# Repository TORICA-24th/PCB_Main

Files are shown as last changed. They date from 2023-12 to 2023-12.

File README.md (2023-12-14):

# PCB_Main
メイン電装部のPCBデータです．24代のメイン電装は2層構成になっており，上層をPCB_Main1,下層をPCB_Main2として設計しています．

# 使用している部品，フットプリント
テキスト印字→◯の部品は基板上にテキスト(ICS-Boardなど)を印字してください．
リファレンス印字→◯の部品は基板上にリファレンス(D1など)を印字してください．
## PCB_Main1
|リファレンス|部品|フットプリント|テキスト印字|リファレンス印字|
|:---:|:---:|:---:|:---:|:---:|
|D1~D8|[整流ダイオード](https://akizukidenshi.com/catalog/g/gI-08327/)|Diode_THT:D_A-405_P10.16mm_Horizontal|✕|✕|
|D9~D14|[LED](https://akizukidenshi.com/catalog/g/gI-06247/)|LED_THT:LED_D5.0mm|◯|✕|
|M78AR05-1~M78AR05-4|[DCDCコンバータ(5V0.5A)](https://akizukidenshi.com/catalog/g/gM-07179/)|Converter_DCDC:Converter_DCDC_RECOM_R-78E-0.5_THT|✕|◯|
|M78AR033-1|[DCDCコンバータ(3.3V0.5A)](https://akizukidenshi.com/catalog/g/gM-07178/)|Converter_DCDC:Converter_DCDC_RECOM_R-78E-0.5_THT|✕|◯|
|XH1~XH6|[XHコネクタ](https://akizukidenshi.com/catalog/g/gC-12842/)|((n)はピン数に合わせて)Connector_JST:JST_XH_S4B-XH-A_1x0(n)_P2.50mm_Horizontal|◯|✕|
|U1|[Raspberry Pi Pico](https://akizukidenshi.com/catalog/g/gM-16132/)|SamacSys_Parts:RPi_Pico_SMD_TH|✕|✕|
|U2|[BNO055](https://akizukidenshi.com/catalog/g/gK-16996/)|AE-BNO055:AE-BNO055|◯|✕|
|U3|[DPS310](https://www.switch-science.com/products/6286)|DPS310:DPS310|◯|✕|
|ICS-Board1|[ICS変換基板](https://www.amazon.co.jp/dp/B07XYZWJGD)|ICS:ICS|✕|✕|
|ICS-SW1A|[トグルスイッチ 3P1回路2接点](https://akizukidenshi.com/catalog/g/gP-12406/)|Connector_PinHeader_2.54mm:PinHeader_1x03_P2.54mm_Vertical|◯|✕|
|C1|[電解コンデンサ](https://akizukidenshi.com/catalog/g/gP-17897/)|Capacitor_THT:CP_Radial_D5.0mm_P2.50mm|✕|◯|

補足  
- 配置は別で送った配置図で指定されているものはそれに従ってください
- 四隅にM3のネジ穴を開けてください

## PCB_Main2
|リファレンス|部品|フットプリント|テキスト印字|リファレンス印字|

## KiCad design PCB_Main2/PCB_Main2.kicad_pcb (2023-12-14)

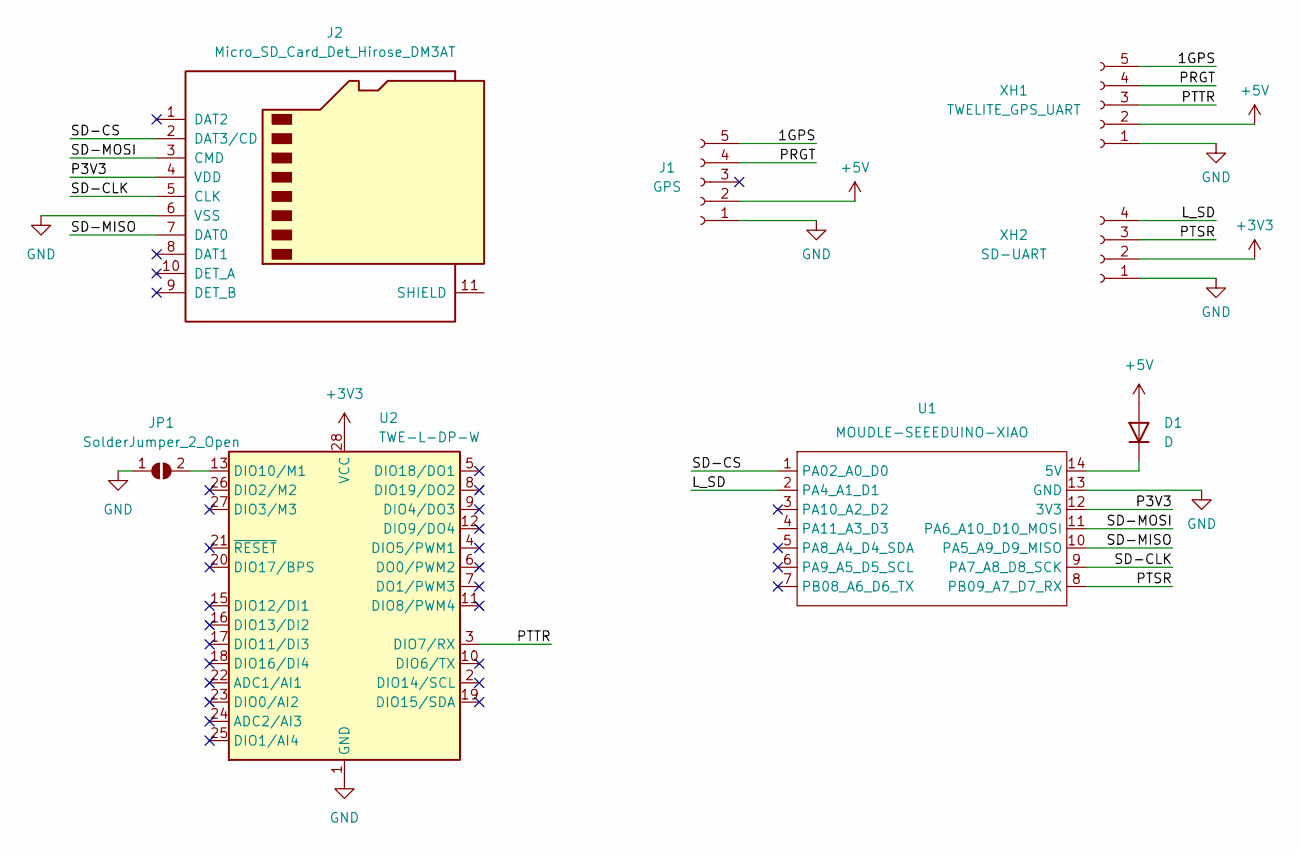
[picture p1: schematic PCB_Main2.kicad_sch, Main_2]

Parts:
D1: D; D_A-405_P10.16mm_Horizontal
J1: GPS; JST_XH_S5B-XH-A_1x05_P2.50mm_Horizontal
J2: Micro_SD_Card_Det_Hirose_DM3AT; microSD_AE-MICRO-SD-DIP
JP1: SolderJumper_2_Open; SolderJumper-2_P1.3mm_Open_RoundedPad1.0x1.5mm
U1: MOUDLE-SEEEDUINO-XIAO; MOUDLE14P-2.54-21X17.8MM
U2: TWE-L-DP-W; DIP-28_W15.24mm
XH1: TWELITE_GPS_UART; JST_XH_S5B-XH-A_1x05_P2.50mm_Horizontal
XH2: SD-UART; JST_XH_S4B-XH-A_1x04_P2.50mm_Horizontal

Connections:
+3V3: U2.28 (VCC), XH2.2
+5V: D1.2 (A), J1.2, XH1.2
/1GPS: J1.5, XH1.5
/L_SD: U1.2 (PA4_A1_D1), XH2.4
/P3V3: J2.4 (VDD), U1.12 (3V3)
/PRGT: J1.4, XH1.4
/PTSR: U1.8 (PB09_A7_D7_RX), XH2.3
/PTTR: U2.3 (DIO7/RX), XH1.3
/SD-CLK: J2.5 (CLK), U1.9 (PA7_A8_D8_SCK)
/SD-CS: J2.2 (DAT3/CD), U1.1 (PA02_A0_D0)
/SD-MISO: J2.7 (DAT0), U1.10 (PA5_A9_D9_MISO)
/SD-MOSI: J2.3 (CMD), U1.11 (PA6_A10_D10_MOSI)
GND: J1.1, J2.6 (VSS), JP1.1 (A), U1.13 (GND), U2.1 (GND), U2.14 (GND), XH1.1, XH2.1
unnamed: D1.1 (K), U1.14 (5V)
unnamed: JP1.2 (B), U2.13 (DIO10/M1)

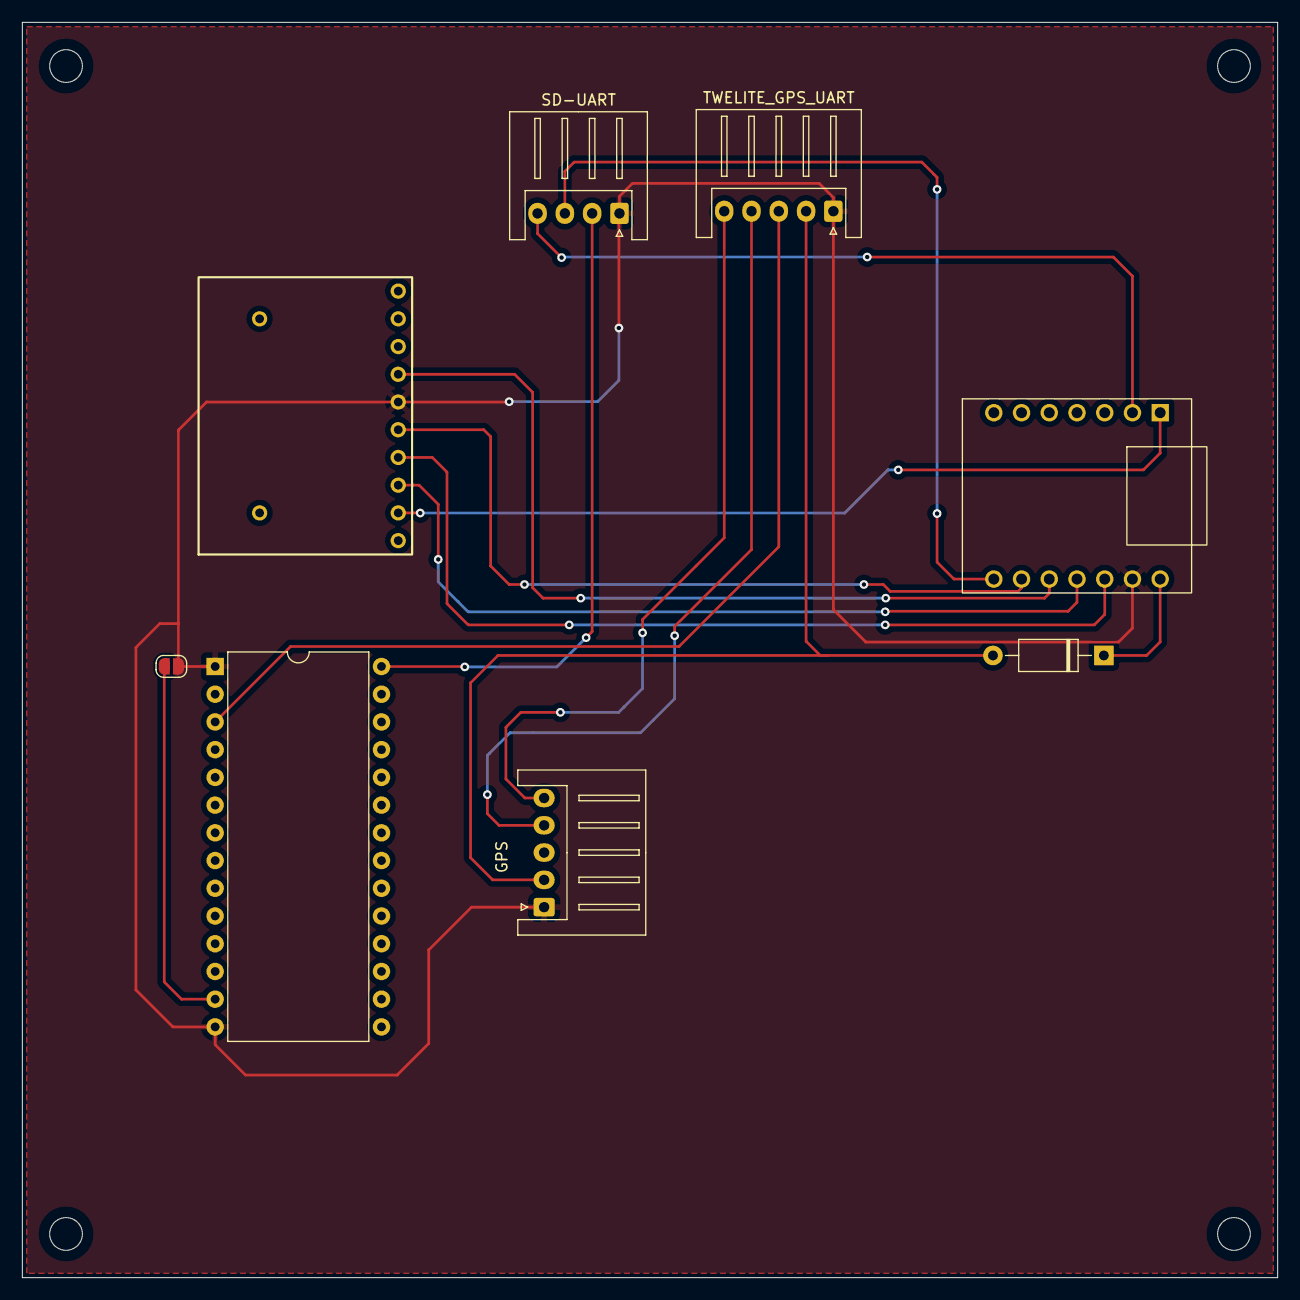
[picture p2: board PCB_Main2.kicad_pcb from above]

Board: 2 copper layers, 115.0 x 115.0 mm, 8 parts (0 on the bottom side), 15 nets.

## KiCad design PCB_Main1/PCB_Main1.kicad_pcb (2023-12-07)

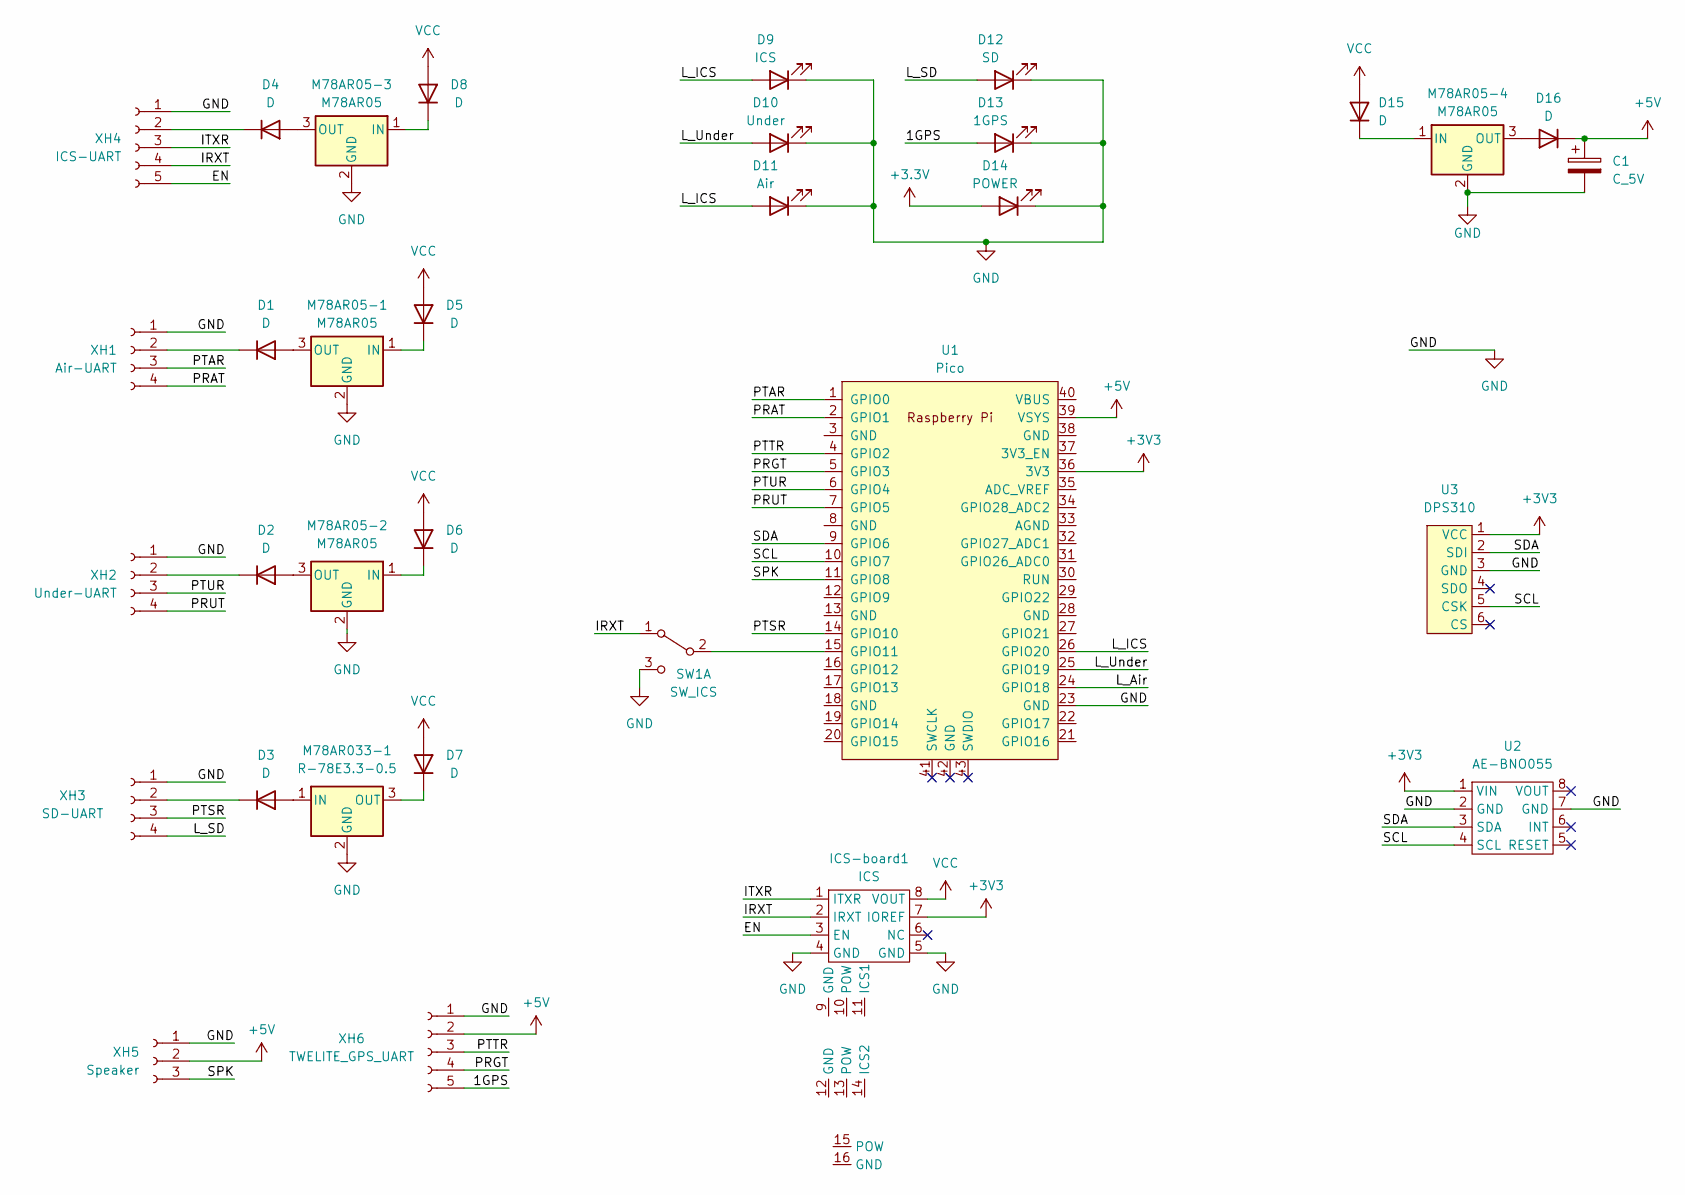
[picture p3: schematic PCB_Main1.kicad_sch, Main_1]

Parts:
C1: C_5V; CP_Radial_D5.0mm_P2.50mm
D1, D2, D3, D4, D5, D6, D7, D8, D15, D16: D; D_A-405_P10.16mm_Horizontal
D9: ICS; LED_D5.0mm
D10: Under; LED_D5.0mm
D11: Air; LED_D5.0mm
D12: SD; LED_D5.0mm
D13: 1GPS; LED_D5.0mm
D14: POWER; LED_D5.0mm
ICS-board1: ICS
M78AR05-1, M78AR05-2, M78AR05-3, M78AR05-4: M78AR05; Converter_DCDC_RECOM_R-78E-0.5_THT
M78AR033-1: R-78E3.3-0.5; Converter_DCDC_RECOM_R-78E-0.5_THT
SW1: SW_ICS; PinHeader_1x03_P2.54mm_Vertical
U1: Pico; RPi_Pico_SMD_TH
U2: AE-BNO055
U3: DPS310
XH1: Air-UART; JST_XH_S4B-XH-A_1x04_P2.50mm_Horizontal
XH2: Under-UART; JST_XH_S4B-XH-A_1x04_P2.50mm_Horizontal
XH3: SD-UART; JST_XH_S4B-XH-A_1x04_P2.50mm_Horizontal
XH4: ICS-UART; JST_XH_S5B-XH-A_1x05_P2.50mm_Horizontal
XH5: Speaker; JST_XH_S3B-XH-A_1x03_P2.50mm_Horizontal
XH6: TWELITE_GPS_UART; JST_XH_S5B-XH-A_1x05_P2.50mm_Horizontal

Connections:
+3.3V: D14.2 (A)
+3V3: ICS-board1.7 (IOREF), U1.36 (3V3), U2.1 (VIN), U3., U3.1 (VCC)
+5V: C1.1, D16.1 (K), U1.39 (VSYS), XH5.2, XH6.2
/1GPS: D13.2 (A), XH6.5
/EN: ICS-board1.3 (EN), XH4.5
/IRXT: ICS-board1.2 (IRXT), SW1.1 (A), XH4.4
/ITXR: ICS-board1.1 (ITXR), XH4.3
/L_Air: U1.24 (GPIO18)
/L_ICS: D9.2 (A), D11.2 (A), U1.26 (GPIO20)
/L_SD: D12.2 (A), XH3.4
/L_Under: D10.2 (A), U1.25 (GPIO19)
/PRAT: U1.2 (GPIO1), XH1.4
/PRGT: U1.5 (GPIO3), XH6.4
/PRUT: U1.7 (GPIO5), XH2.4
/PTAR: U1.1 (GPIO0), XH1.3
/PTSR: U1.14 (GPIO10), XH3.3
/PTTR: U1.4 (GPIO2), XH6.3
/PTUR: U1.6 (GPIO4), XH2.3
/SCL: U1.10 (GPIO7), U2.4 (SCL), U3.5 (CSK)
/SDA: U1.9 (GPIO6), U2.3 (SDA), U3.2 (SDI)
/SPK: U1.11 (GPIO8), XH5.3
GND: C1.2, D9.1 (K), D10.1 (K), D11.1 (K), D12.1 (K), D13.1 (K), D14.1 (K), ICS-board1.4 (GND), ICS-board1.5 (GND), M78AR05-1.2 (GND), M78AR05-2.2 (GND), M78AR05-3.2 (GND), M78AR05-4.2 (GND), M78AR033-1.2 (GND), SW1.3 (C), U1.23 (GND), U2.2 (GND), U2.7 (GND), U3.3 (GND), XH1.1, XH2.1, XH3.1, XH4.1, XH5.1, XH6.1
unnamed: D1.2 (A), M78AR05-1.3 (OUT)
unnamed: D1.1 (K), XH1.2
unnamed: D2.2 (A), M78AR05-2.3 (OUT)
unnamed: D2.1 (K), XH2.2
unnamed: D3.2 (A), M78AR033-1.1 (IN)
unnamed: D3.1 (K), XH3.2
unnamed: D4.2 (A), M78AR05-3.3 (OUT)
unnamed: D4.1 (K), XH4.2
unnamed: D5.1 (K), M78AR05-1.1 (IN)
unnamed: D6.1 (K), M78AR05-2.1 (IN)
unnamed: D7.1 (K), M78AR033-1.3 (OUT)
unnamed: D8.1 (K), M78AR05-3.1 (IN)
unnamed: D15.1 (K), M78AR05-4.1 (IN)
unnamed: D16.2 (A), M78AR05-4.3 (OUT)
unnamed: SW1.2 (B), U1.15 (GPIO11)
VCC: D5.2 (A), D6.2 (A), D7.2 (A), D8.2 (A), D15.2 (A), ICS-board1.8 (VOUT)

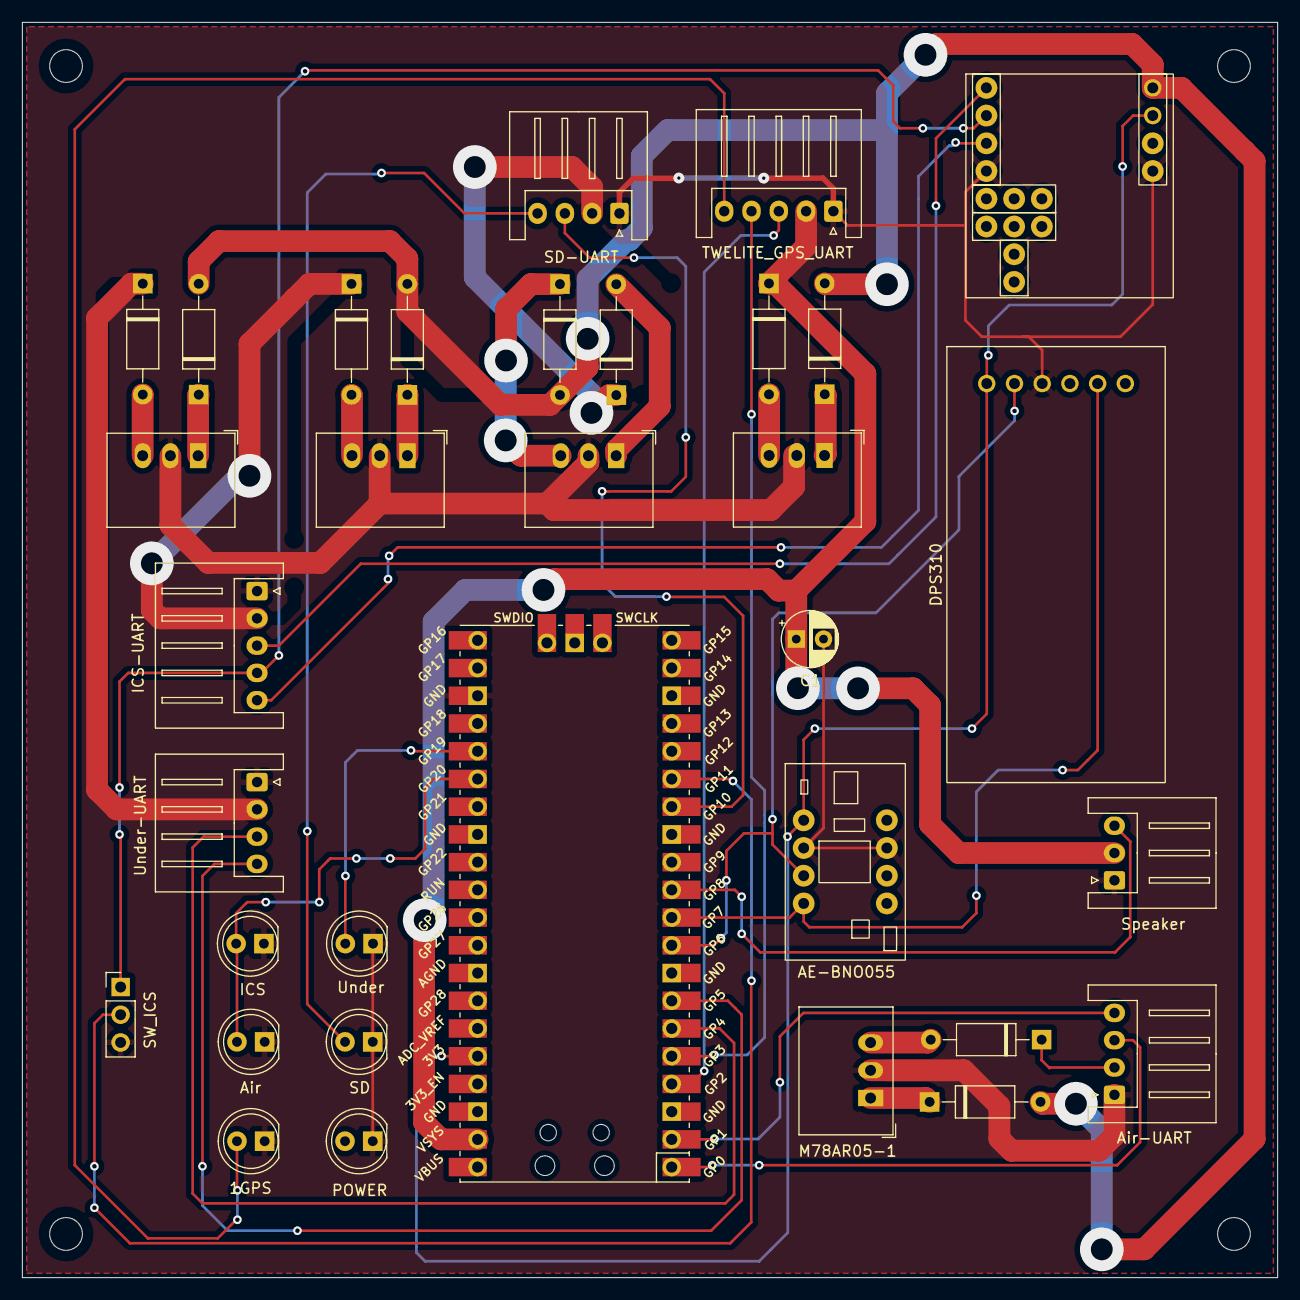
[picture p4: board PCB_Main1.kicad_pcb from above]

Board: 2 copper layers, 115.0 x 115.0 mm, 33 parts (0 on the bottom side), 36 nets.

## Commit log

2023-11-03 update PCB_Main1.sch(1st create)
    1st create
    [PCB_Main-B_Cu.gbr, PCB_Main-B_Mask.gbr, PCB_Main-B_Paste.gbr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]
2023-11-03 Do annotation
    [PCB_Main1.kicad_sch, PCB_Main2.kicad_sch]
2023-11-03 update PCB_Main1 & PCB_Main2
    [PCB_Main1.kicad_sch, PCB_Main2.kicad_sch]
2023-11-07 add gyro sensor
    [PCB_Main1.kicad_sch]
2023-11-17 Update PCB_Main
    [PCB_Main1.kicad_pcb, PCB_Main1.kicad_sch, PCB_Main2.kicad_sch]
2023-12-14 add backup
    [PCB_Main1.kicad_sch]
